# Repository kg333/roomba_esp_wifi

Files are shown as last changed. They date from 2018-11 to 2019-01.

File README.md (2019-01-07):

# roomba_esp_wifi
Board for adding wifi using ESP-12 to Roomba 500/600 series.

## Overview

This project describes a board with an ESP-12 microcontroller and the following interfaces:
* UART - 3.3V, 5.0V tolerant
* Battery input - supports 4.75V - 36V
* GPIO - single pin at 3.3V
* 3.3V auxiliary output

It is intended for use with [esp-roomba-mqtt by John Boiles](https://github.com/johnboiles/esp-roomba-mqtt), but may also be suitable for general use in battery-powered applications.

## Layout
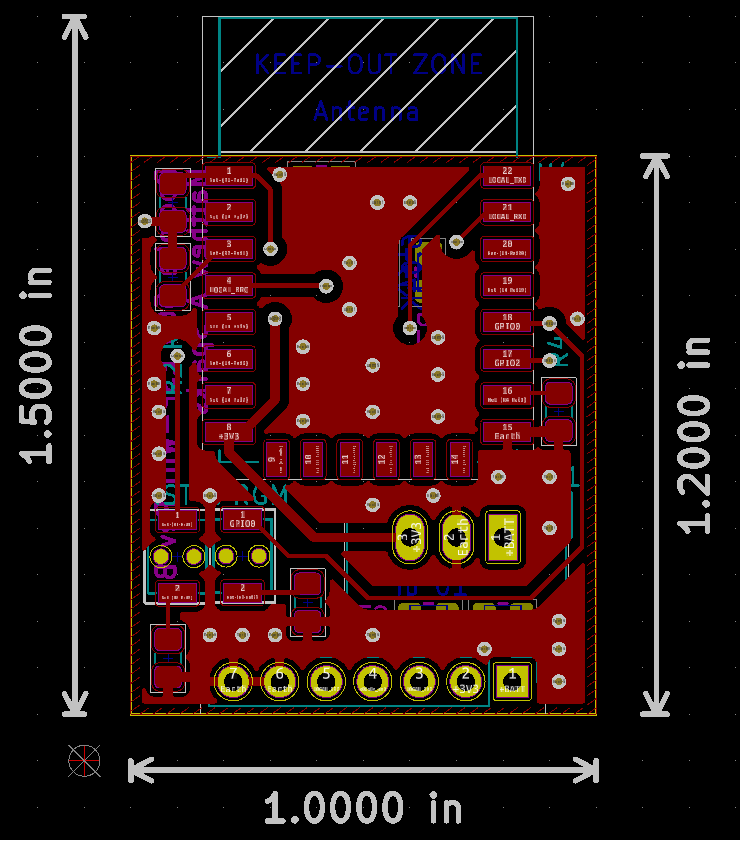
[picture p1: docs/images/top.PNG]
Board, top
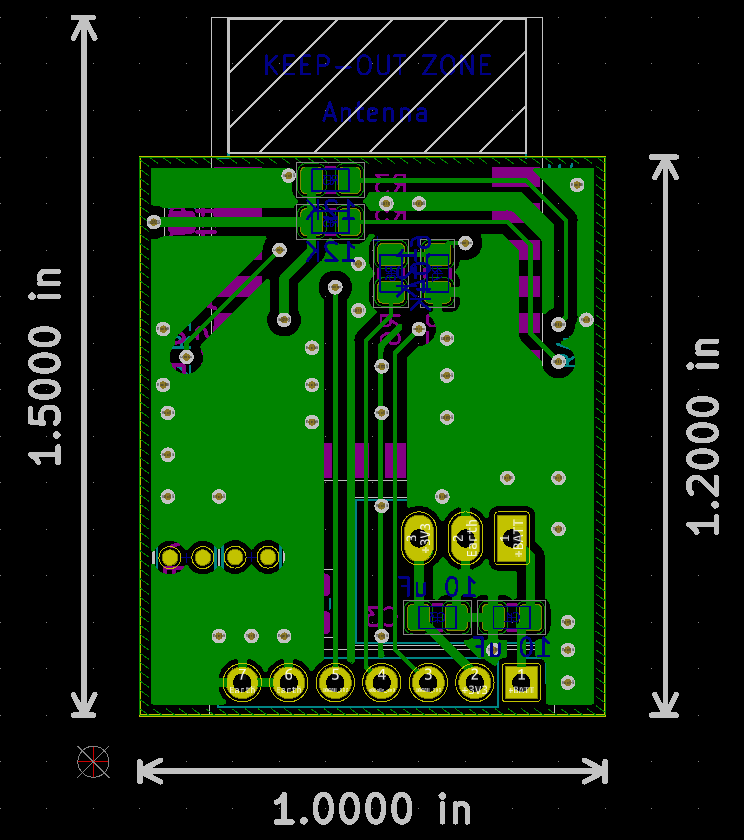
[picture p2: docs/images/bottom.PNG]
Board, bottom
 

## Parts

| Quantity | Part Description | Suggested Part Number |
| --- | --- | --- |
| 1 | ESP-12E or ESP-12F | N/A |
| 2 | Small push buttons | PTS820J15MSMTRLFS |
| 2 | Resistor, 470Ω, 0805 | ERJ-6ENF4700V |
| 6 | Resistor, 12KΩ, 0805 | ERJ-6ENF1182V |
| 1 | Resistor, 6.04KΩ, 0805 | ERJ-6ENF6041V |
| 2 | Capacitor, 10µF, 0805  | C0805C106K3PAC7800 |
| 1 | 1x7 100mil header (optional) | PPPC071LFBN-RC |
| 1 | 3.3V DC-DC Converter | TSR 1-2433 |

## Programming

This board can be intially programmed in a similar fashion to a NodeMCU using your preferred Arduino programmer, but does require manual control using the PRGM and RST buttons.  If using esp-roomba-mqtt, it may be programmed over Wifi after the initial flash.

## Installation

The board is designed to fit inside a Roomba 560 behind the starboard wheel well.  It is recommended to solder wires between the board and the rear of the Roomba Mini-DIN port to avoid having a Mini-DIN plug sticking up from the Roomba.

### Installation location on Roomba 560
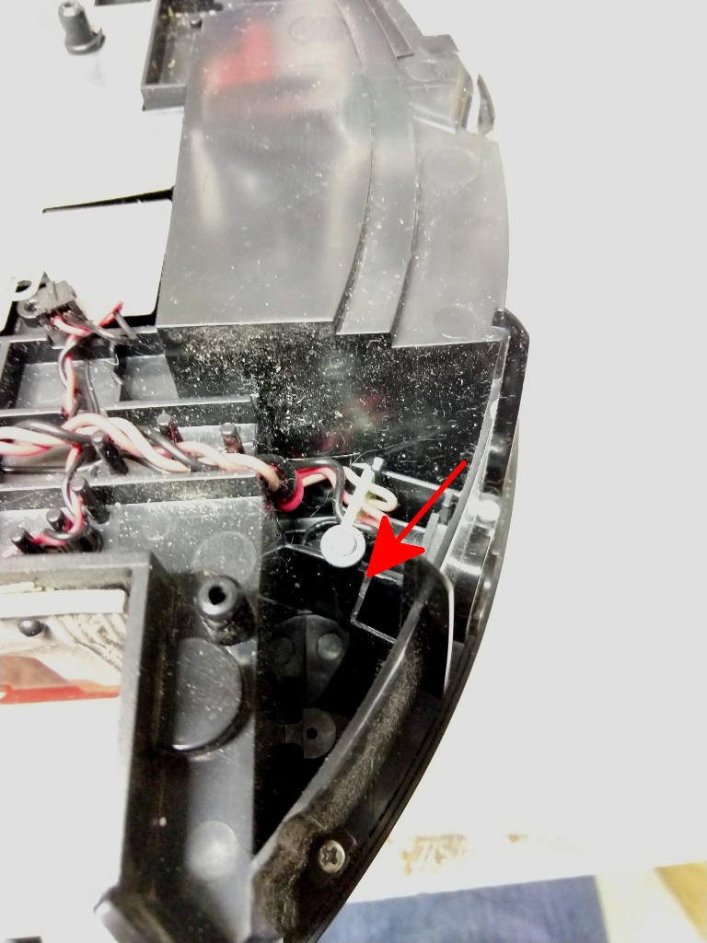
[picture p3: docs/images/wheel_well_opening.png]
Wheel well starboard opening

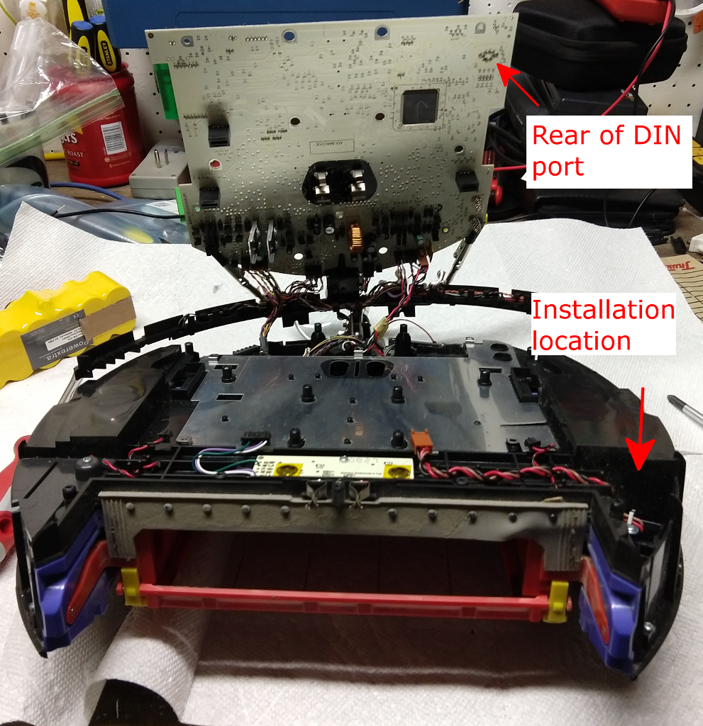
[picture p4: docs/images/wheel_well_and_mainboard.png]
Wheel well starboard opening and rear of DIN connector

### Board wired in
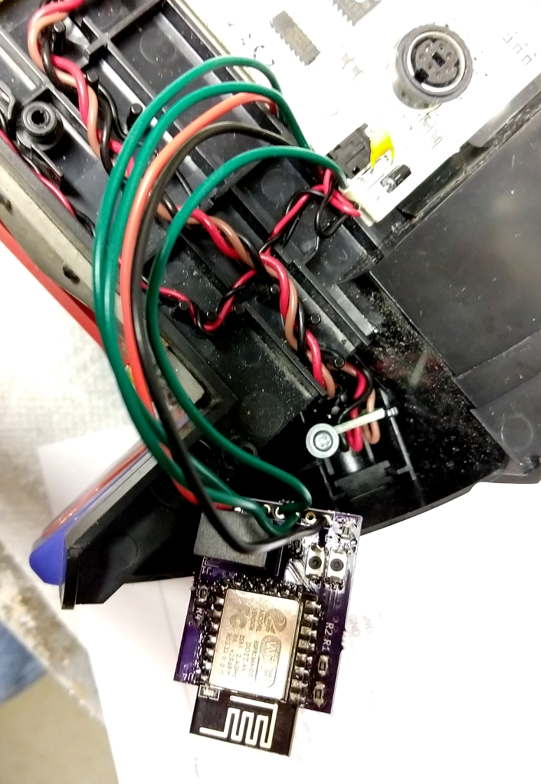
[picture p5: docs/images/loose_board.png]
Board after soldering connections

### Final installation
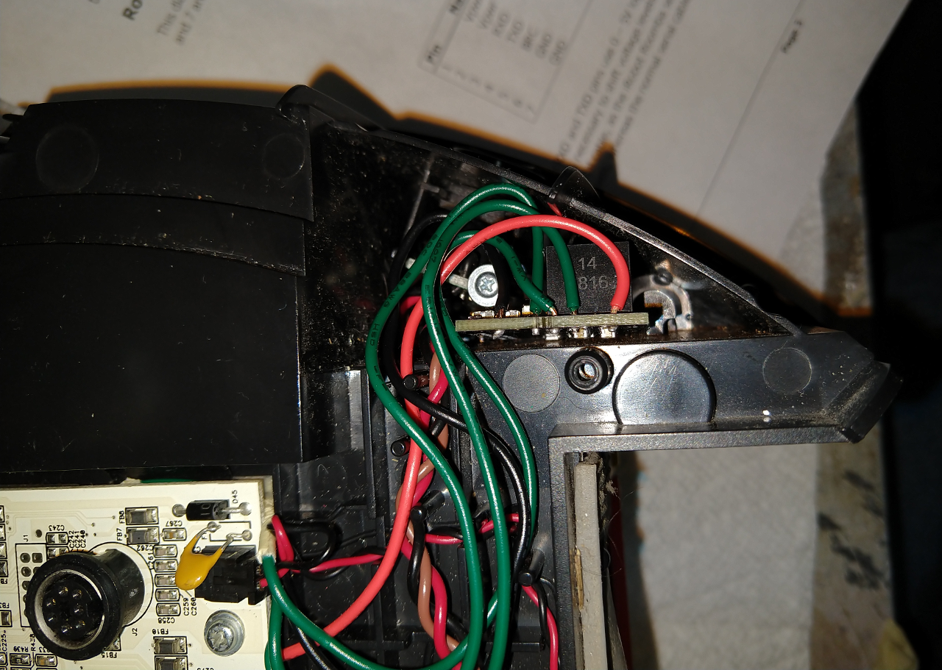
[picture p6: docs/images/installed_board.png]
Board installed in wheel wells


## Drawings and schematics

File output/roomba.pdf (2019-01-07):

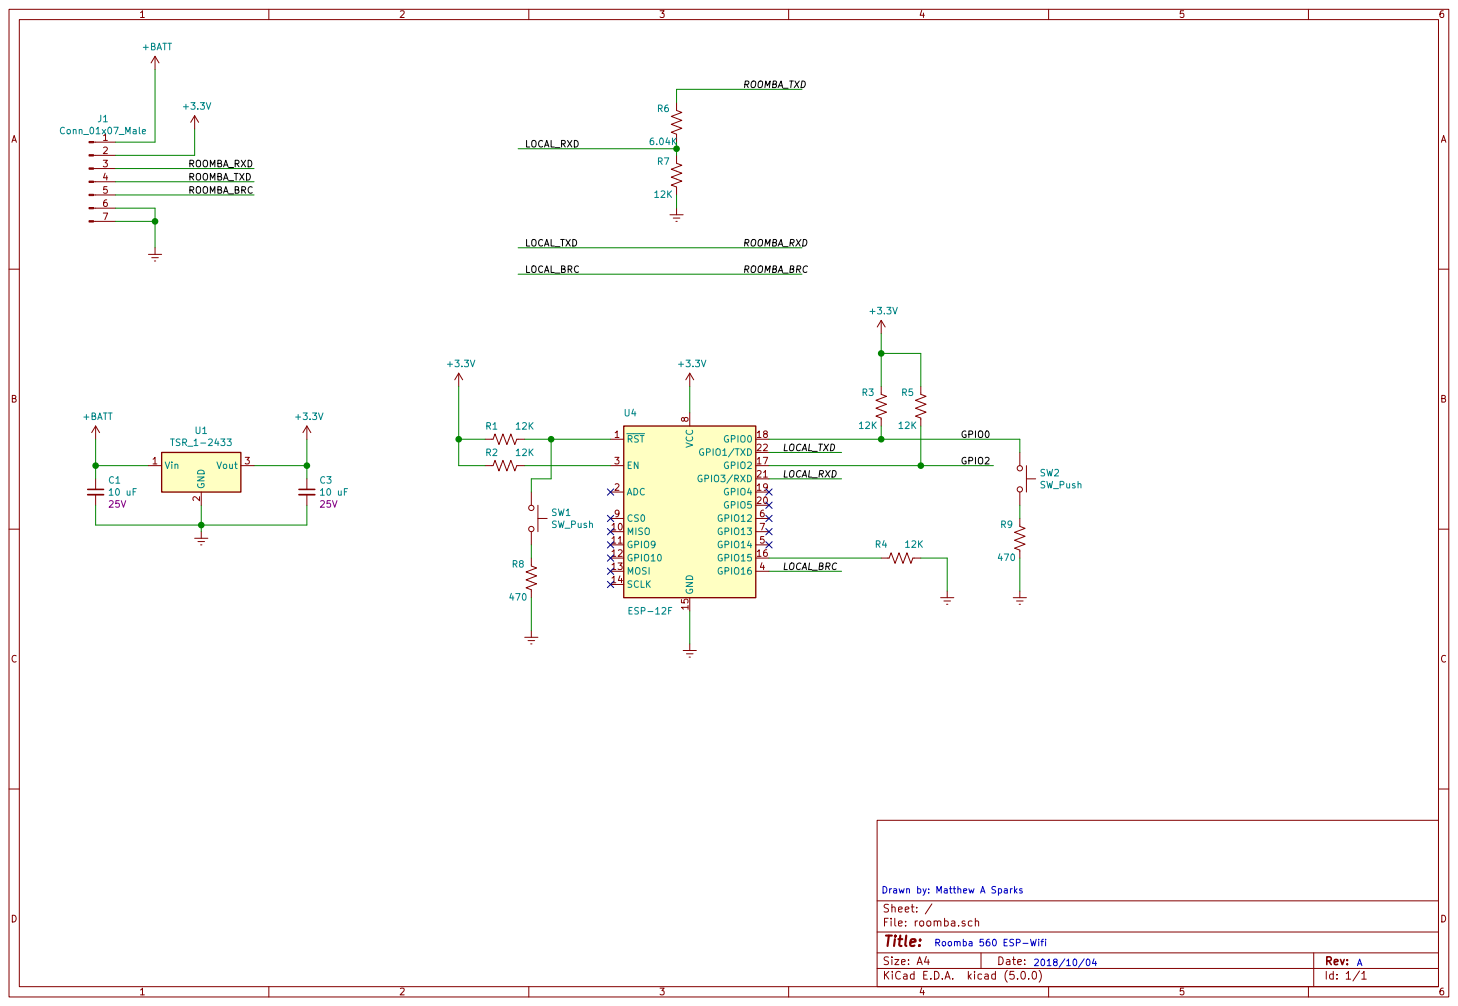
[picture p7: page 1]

Id: 1/1 Title: File: roomba.sch Sheet: /

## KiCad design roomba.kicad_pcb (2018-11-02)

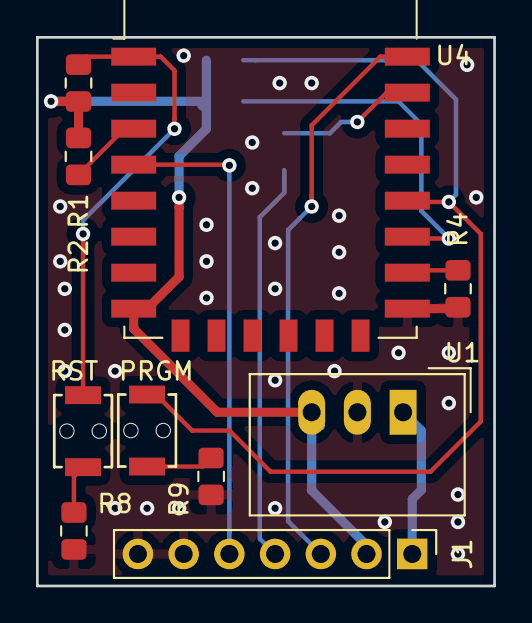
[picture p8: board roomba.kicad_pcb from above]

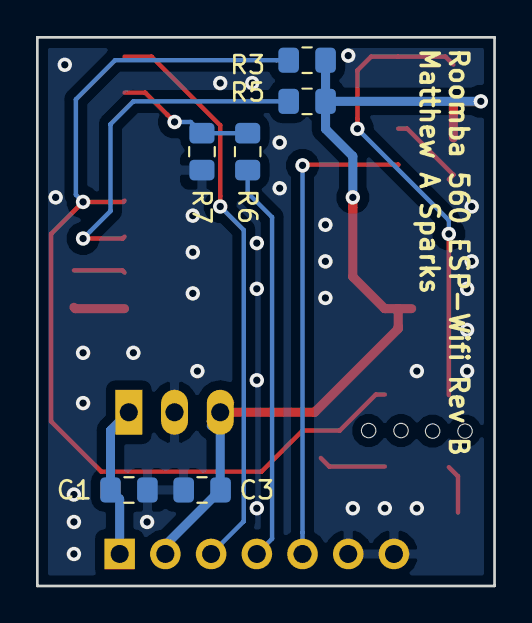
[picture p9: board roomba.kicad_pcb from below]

Board: 2 copper layers, 25.4 x 30.5 mm, 16 parts (6 on the bottom side), 14 nets.

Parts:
C1, C3: 10 uF; C_0805_2012Metric_Pad1.15x1.40mm_HandSolder
J1: Conn_01x07_Male; PinHeader_1x07_P2.54mm_Vertical
PRGM: SW_Push; PTS820
R1, R2, R3, R4, R5, R7: 12K; R_0805_2012Metric_Pad1.15x1.40mm_HandSolder
R6: 6.04K; R_0805_2012Metric_Pad1.15x1.40mm_HandSolder
R8, R9: 470; R_0805_2012Metric_Pad1.15x1.40mm_HandSolder
RST: SW_Push; PTS820
U1: TSR_1-2433; Converter_DCDC_TRACO_TSR-1_THT
U4: ESP-12F; ESP-12E

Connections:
+3V3: C3.1, J1.2, R1.2, R2.2, R3.2, R5.2, U1.3, U4.8
+BATT: C1.1, J1.1, U1.1
/GPIO0: PRGM.1, R3.1, U4.18
/GPIO2: R5.1, U4.17
/LOCAL_BRC: J1.5, U4.4
/LOCAL_RXD: R6.1, R7.2, U4.21
/LOCAL_TXD: J1.3, U4.22
/ROOMBA_TXD: J1.4, R6.2
Earth: C1.2, C3.2, J1.6, J1.7, R4.2, R7.1, R8.1, R9.1, U1.2, U4.15
unnamed: R1.1, RST.1, U4.1
unnamed: R2.1, U4.3
unnamed: R4.1, U4.16
unnamed: R8.2, RST.2
unnamed: PRGM.2, R9.2

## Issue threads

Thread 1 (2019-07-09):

new schematics

pilot1981, 2019-07-09:
Hi,
you suggested to use resistor and capacitor different form johnboiles, hoot you suggest to use them?

can you share schematics?

kg333, 2019-09-12:
Sorry about the slow reply; I didn't get a notification for this.  I'm not certain what difference from John's schematics you're asking about, but schematics are included in the repo.  Just open in KiCAD 6.0.

Closed 2019-09-12.

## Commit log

2018-08-30 Initial prototype for Roomba wifi circuit
    [roomba.kicad_pcb, roomba.sch]
2018-09-09 Adding Roomba dev board schematic output
2018-10-05 Updating circuit for Roomba PCB part placement complete
    Adding ESP8266 part libraries
    [roomba.kicad_pcb, roomba.sch]
2018-10-05 Routed PCB for Roomba
    [roomba.kicad_pcb, roomba.sch]
2018-10-05 Adding silkscreen and title/date information.
    [roomba.kicad_pcb]
2018-10-05 Updated layout to a 1 by 1.2 inch size. Components are now on both sides. Solder Mask Clearance adjusted to 0.002in
    [roomba.kicad_pcb]
2018-10-22 Removed TXB0104, since it was garbling UART. Instead added voltage divider on TXD from Roomba, and ran RXD and BRC to Roomba directly.
    [roomba.kicad_pcb, roomba.sch]
2018-11-02 Updating Roomba project to use buttons for reset/programming. Removing 5V to 3.3V translator in favor of voltage divider. Removing 5V to 3.3V regulator and going directly from BATT to 3.3V.
    [roomba.kicad_pcb, roomba.sch]
2019-01-07 Updating documentation and adding licensing for this project and kicad-ESP8266 by jdunmire.
